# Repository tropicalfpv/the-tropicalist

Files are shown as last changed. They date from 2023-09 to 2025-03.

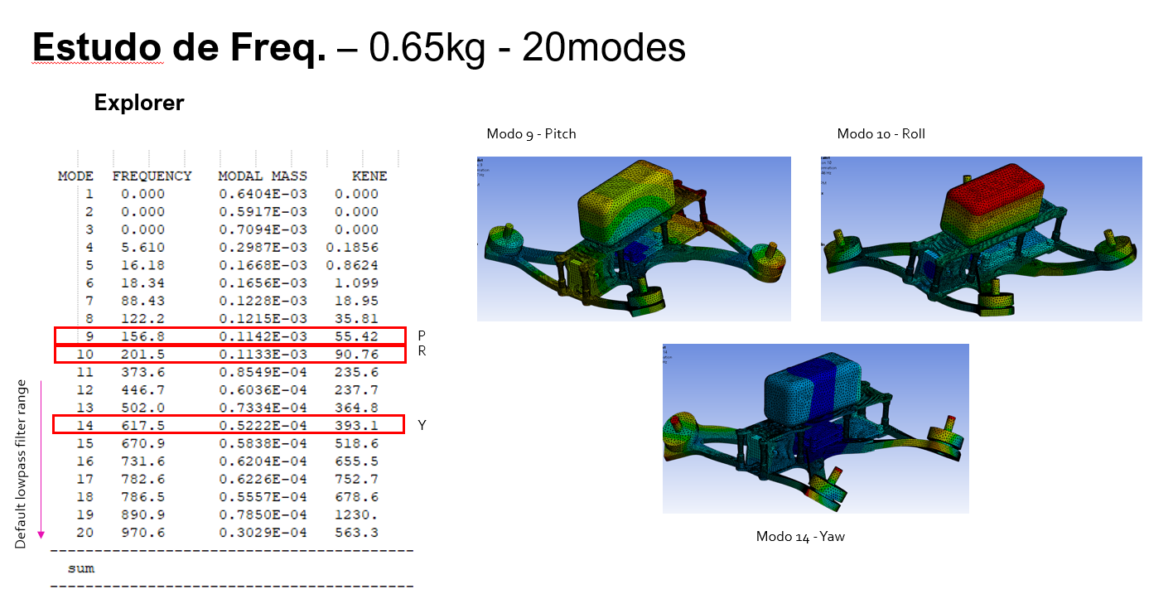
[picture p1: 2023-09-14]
Project/FEA Analysis/freq.PNG

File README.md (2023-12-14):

Capture

# The Tropicalist 5" FPV Open Source Frame Kit :bird:
Developed to be the best FPV frame in the world, no matter what is your application. Born in Brazil. Join the community for support, news, and other major releases, as well as to get help during your development [in our discord][7].

*PT_BR: Se você quer entender melhor do frame assim como seus aspectos principais, em portugês, acesse www.tropicalfpv.com*



## Quick Notice :dollar:
This project was initially close-source. We opened to be part of a greater achievement for the FPV community, as well as to expand reach and dissipate knowledge. By doing so, we lost a great share of revenue. To support its constant evolution, [consider a donation][1].

## Short Read :envelope:
This frame was developed to be easily assembled, strong, and accessible for any 5' FPV build. Focused on having a better performance than traditional frames concerning resonant frequencies, it is a great build for cinematics and freestyle pilots. 
1. Start by downloading the latest files under the [Releases][5] page,
2. You can order the parts to construct the frame using this [Bill of Materials and Ordering Instructions][6],
3. Follow the [instructions for fabrication][4]

## Long Read :book:

### Objectives and Configuration :dart:
The Tropicalist Frame Kit was initially developed in 2020 during the pandemic, during which a great flow of imports in Brazil was frozen. To keep the FPV rolling here, we needed a frame that could be strong enough to withstand the tropical bandos and also cinematic ready, since a new era of pilots was born.

The Frame is a perfect X configuration, has 5mm arms, and is designed for up to 5.1in props. It has enough space for analog and digital builds and it's designed to carry a camera on top, as well as a 4s-6s battery.

For the Frame to perform at its best, is expected that fabrication using 3K plain matte carbon, from a good supplier is used. If you are using other composites or materials be aware that it can be extremely poor on performance, since the materials' mechanical properties are key in this design.

### Editing and Modifying the Files :rocket:
You can modify and download the original Autodesk Fusion 3D Files. Those are available [here][8]. If you want to consider collaborating on this project, [please follow the guidelines here for contributing][2], and our step-by-step process to have PRs accepted.

### Scientific-Based Research :microscope:
The Tropicalist Frame is based on scientific research to approach a feasible, high-frequency resonant frame. It is also tested in Structural FEA Analysis Software (such as Ansys Mechanical) before being released. All major changes should include a FEA Analysis and field testing before being considered a new release under the main branch. We do this to guarantee the highest standard in design quality and best practices, so users and the community can rely on a frame without being super nerds about mechanical aspects. They just trust, and that´s enough :)



freq

## Licenses & Right to Use :closed_lock_with_key:
This project is licensed under the [Creative Commons Attribution-ShareAlike 4.0 International Public License][3]. This means that you can use, modify, and benefit from the project, including commercial use. This license, however, obligates you or any party to maintain the name of the product as copywriting and share any projects related to it under the same Open Source License. This means that if you use in part of your design, yours needs to be open source too.

## Found a Problem? :goberserk:
It's ok, you don't need to fix it, you can let us know to do so. Just [open an Issue here][9] and be detailed about what happened. 

[1]: https://patreon.com/TropicalFPV
[2]: https://github.com/tropicalfpv/the-tropicalist/blob/main/GUIDELINES.md
[3]: https://github.com/tropicalfpv/the-tropicalist/blob/main/LICENSE
[4]: https://github.com/tropicalfpv/the-tropicalist/blob/main/ASSEMBLY.md
[5]: https://github.com/tropicalfpv/the-tropicalist/releases
[6]: https://github.com/tropicalfpv/the-tropicalist/blob/main/BOM.md
[7]: https://discord.gg/JvUaVDHNnM
[8]: https://github.com/tropicalfpv/the-tropicalist/tree/main/Project/Fusion%203D%20Files
[9]: https://github.com/tropicalfpv/the-tropicalist/issues/new

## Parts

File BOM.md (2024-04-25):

# Bill of Materials and Ordering Instructions
You can buy using your favorite store/supplier. We recommend the following ones:
Please note that these are affiliate links. By using them, you help to support the project with a commission that has no additional cost to you :)

## Frame Cut Parts
Good-quality carbon is a must! We recommend Sunlike because they offer ready cuts, and use a great fiber+resin mix (3k plain matte). Email info@sunlikeec.com with a zip of the ['Latest Release of the Carbon Cut Files'][1] for a quote and then use this link to pay after the quote is sent to you: https://s.click.aliexpress.com/e/_Dlow8zd. You should select the amount of dollars that were quoted as the quantity of the items since each one is exactly one dollar. **You can also pay by PayPal, so you don't get a big amount in Aliexpress (mainly for Brazilian customers). Ask Sunlike for the instructions in your email**

PT_BR: Para detalhes sobre como comprar sem uma taxa abusiva do Remessa Conforme, me chame no insta @tropical.fpv

Example email asking for a quote:



## Hardware Parts
If you are using the affiliate links, please select the correct part after you are redirected.

- 8x M3x14mm Hex (https://s.click.aliexpress.com/e/_Dn0yasj)
- 8x M3x6mm Hex (https://s.click.aliexpress.com/e/_Dn0yasj)
- 4x M3x20mm Flathead Hex (stack option 1) (https://s.click.aliexpress.com/e/_DnrfiV5) 
- 4x M3x8mm Flathead Hex (stack option 2) (https://s.click.aliexpress.com/e/_DnrfiV5)
- 4x M3x16mm Hex (https://s.click.aliexpress.com/e/_Dn0yasj)
- 16x M3x8mm Hex (Motor Screws) (https://s.click.aliexpress.com/e/_DksbGjv)
- 4x 4x M3x6mm Flathead Hex (https://s.click.aliexpress.com/e/_DnrfiV5)
- 4x M3x30mm 6mm diameter Aluminium standoff (https://s.click.aliexpress.com/e/_DC3XDLV)
- 4x M3x35mm 6mm diameter Aluminium standoff (https://s.click.aliexpress.com/e/_DC3XDLV)
- 8x M3 Parlock Nut (https://s.click.aliexpress.com/e/_DDdlpIF)

## Cost (US Dollar)
The biggest cost is of the carbon fiber plates, mainly the arms.
- Carbon plates (entire kit for one frame): ~$58,00
- Hardware Kit (Standoffs): ~$6,00
- Hardware Kit (Screws): $5,00
- 3D printed parts: ~$8,00
- Shipping (CN to BR): ~$10,00
**Total Cost approximated is ~$89,00**

Depending on where you live, this can range up and down by about 15%.

[1]: [https://github.com/tropicalfpv/the-tropicalist/releases]

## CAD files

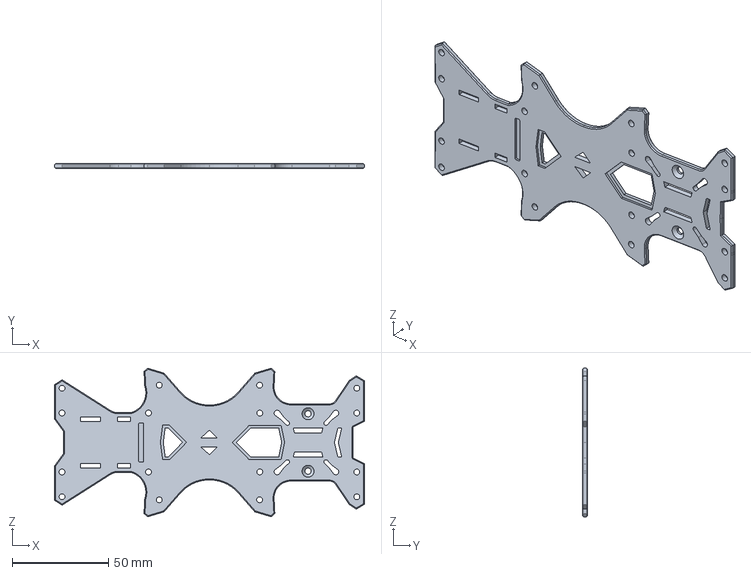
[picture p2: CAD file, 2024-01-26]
Project/Carbon Cut Files/2.5mm cut/bottom_plate_x1.step
161.3 x 2.50 x 77.3 mm

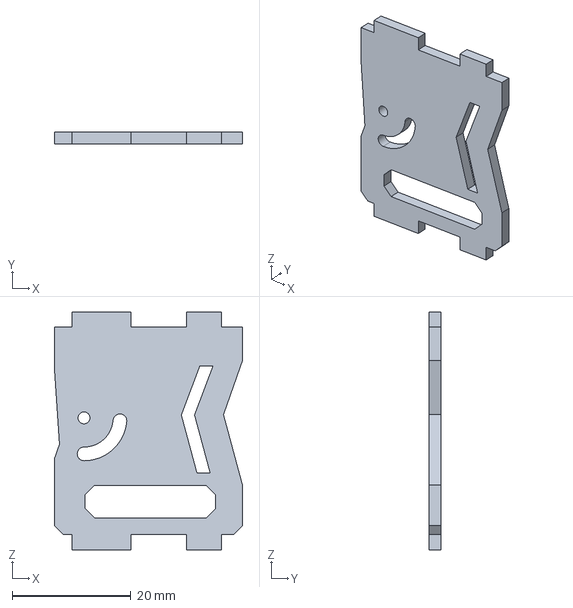
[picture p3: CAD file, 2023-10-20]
Project/Carbon Cut Files/2mm cut/camera_mount_side_plate_x2.step
31.7 x 2.00 x 40.1 mm

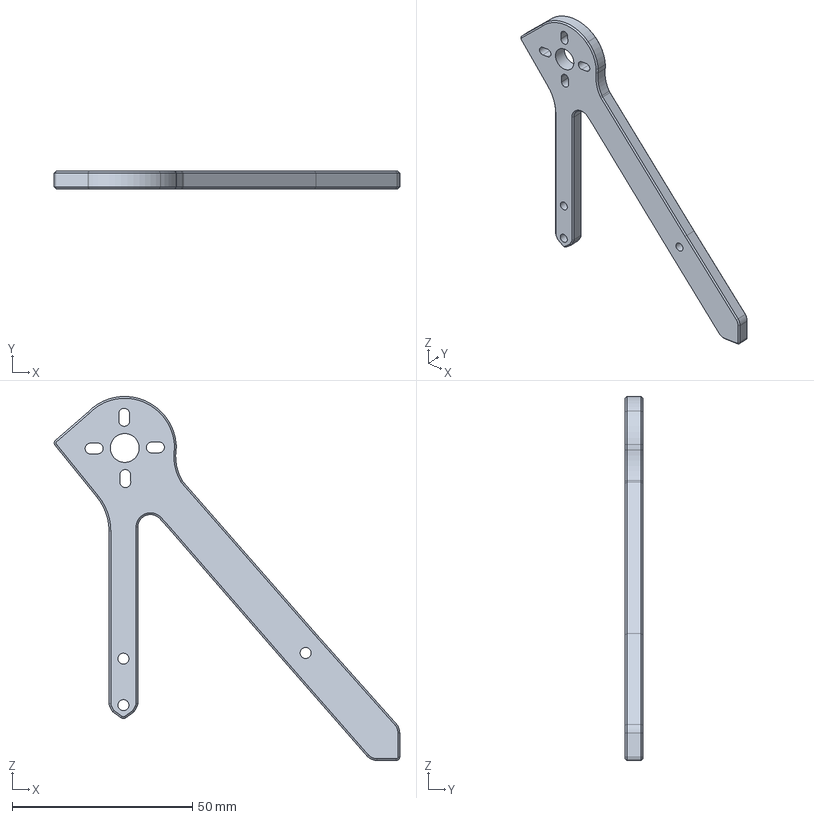
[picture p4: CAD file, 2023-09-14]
Project/Carbon Cut Files/5mm cut/arm_x4.step
95.9 x 5.00 x 101.0 mm

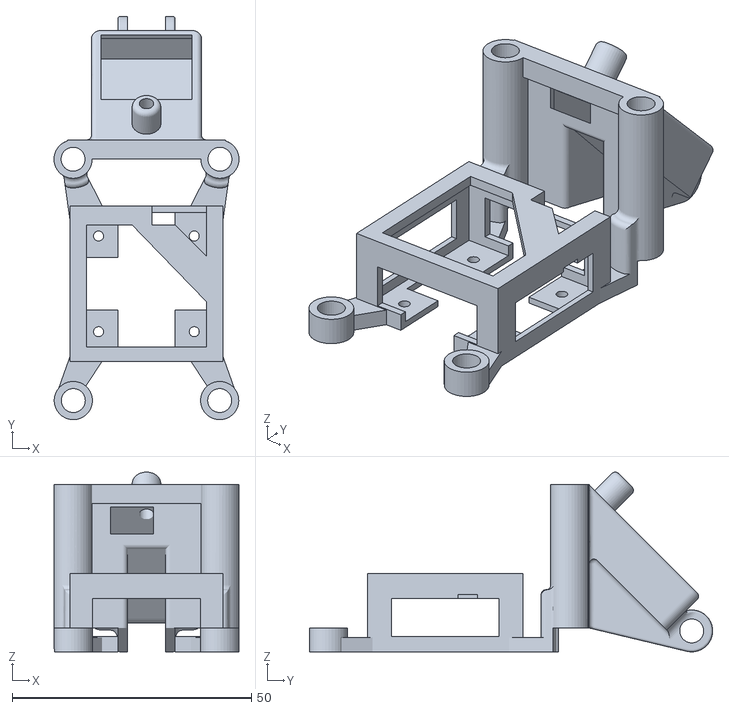
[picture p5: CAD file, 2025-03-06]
Project/STL Files/caddx_and_gpshold.STL
38.7 x 84.3 x 37.6

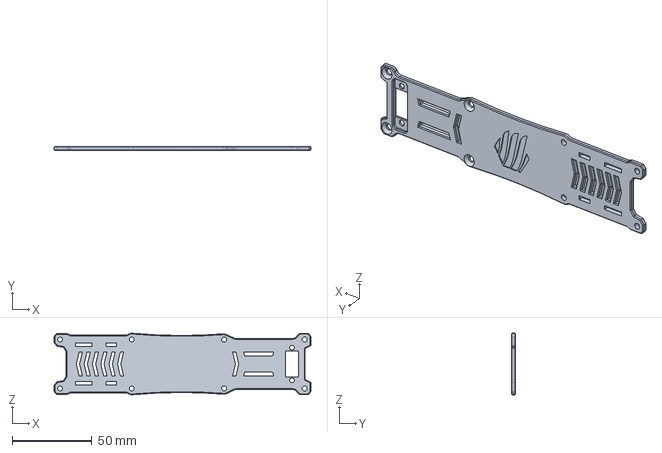
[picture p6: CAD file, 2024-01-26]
Project/Carbon Cut Files/2.5mm cut/top_plate_x1.step
161.2 x 2.50 x 38.7 mm

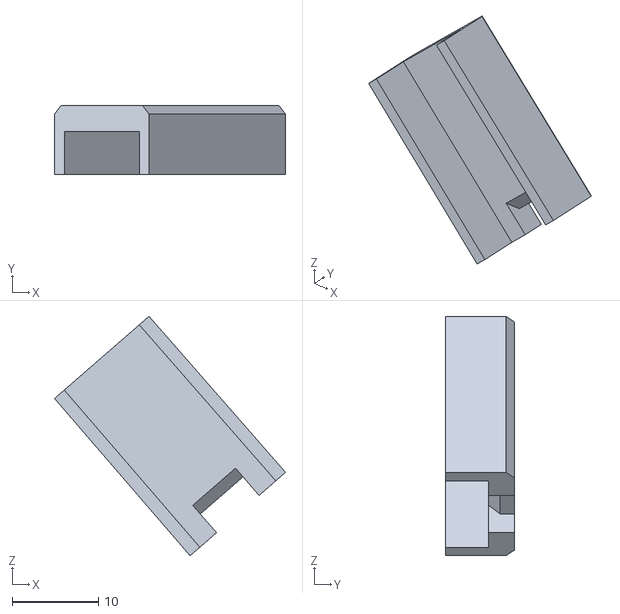
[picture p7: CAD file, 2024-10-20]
Project/STL Files/motor_wire_protector.stl
26.7 x 8.00 x 27.7

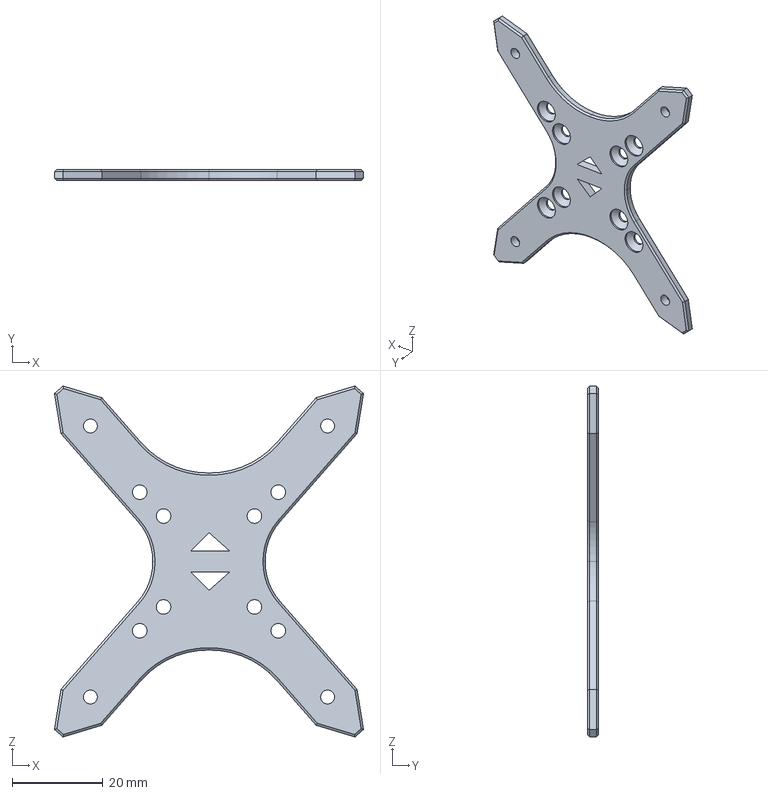
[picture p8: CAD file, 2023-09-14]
Project/Carbon Cut Files/2.5mm cut/middle_plate_x1.step
68.1 x 2.50 x 77.3 mm

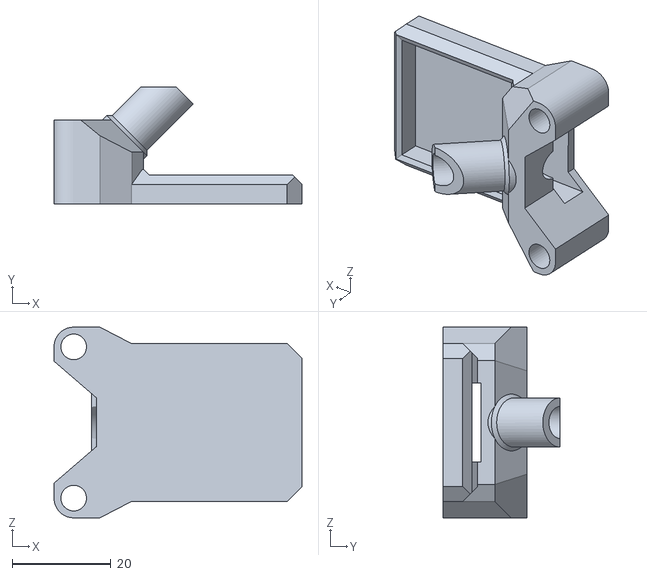
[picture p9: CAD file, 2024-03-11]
Project/STL Files/gps_antenna_mount_O3.stl
50.3 x 23.7 x 38.7

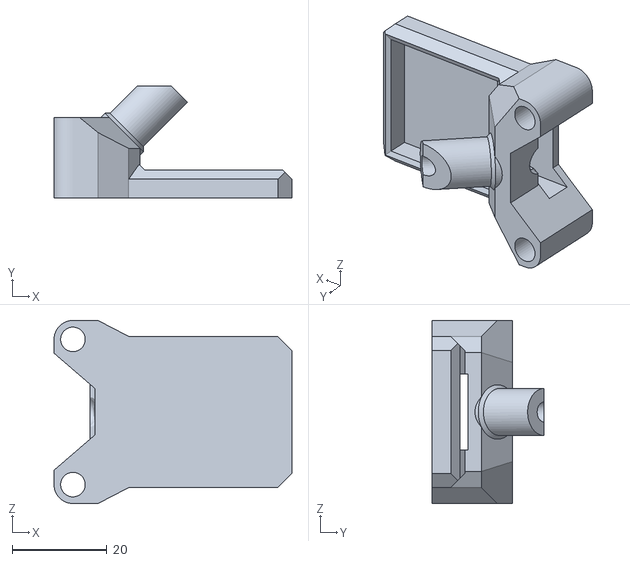
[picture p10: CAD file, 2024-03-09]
Project/STL Files/gps_antenna_mount_caddx_vista.stl
50.3 x 23.7 x 38.7

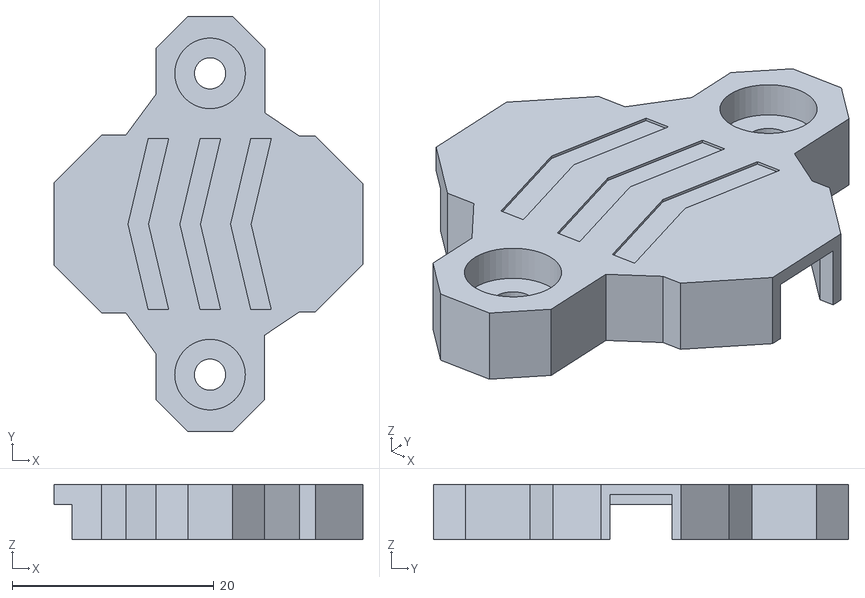
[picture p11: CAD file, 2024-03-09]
Project/STL Files/rx_holder_botom.stl
30.6 x 41.2 x 5.50

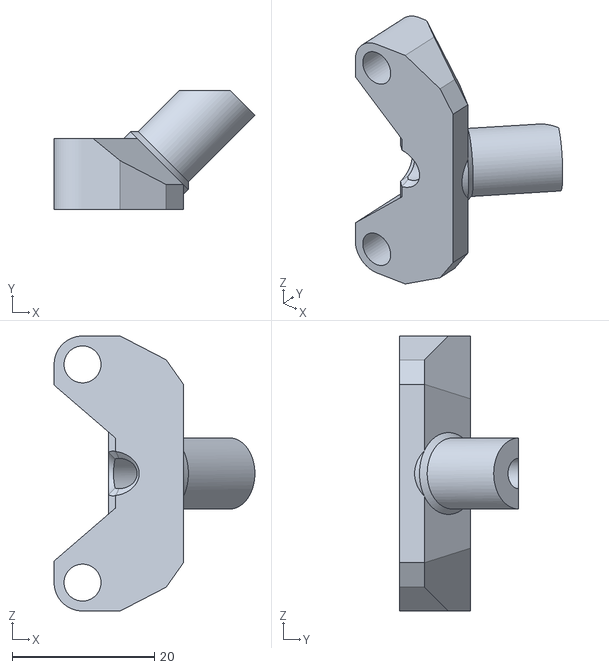
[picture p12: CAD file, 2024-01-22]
Project/STL Files/antenna_mount_caddx_vista.stl
28.3 x 16.7 x 38.7

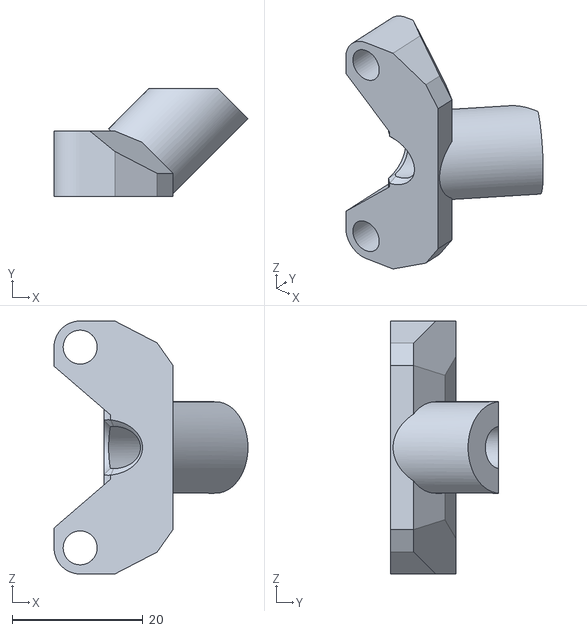
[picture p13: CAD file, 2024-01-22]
Project/STL Files/antenna_mount_O3.stl
29.7 x 16.5 x 38.7

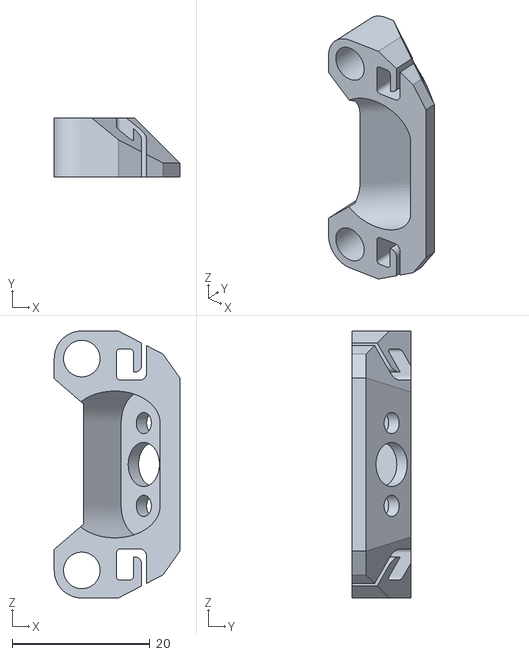
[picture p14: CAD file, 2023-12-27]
Project/STL Files/antenna_mount_sma.stl
18.2 x 8.50 x 38.7

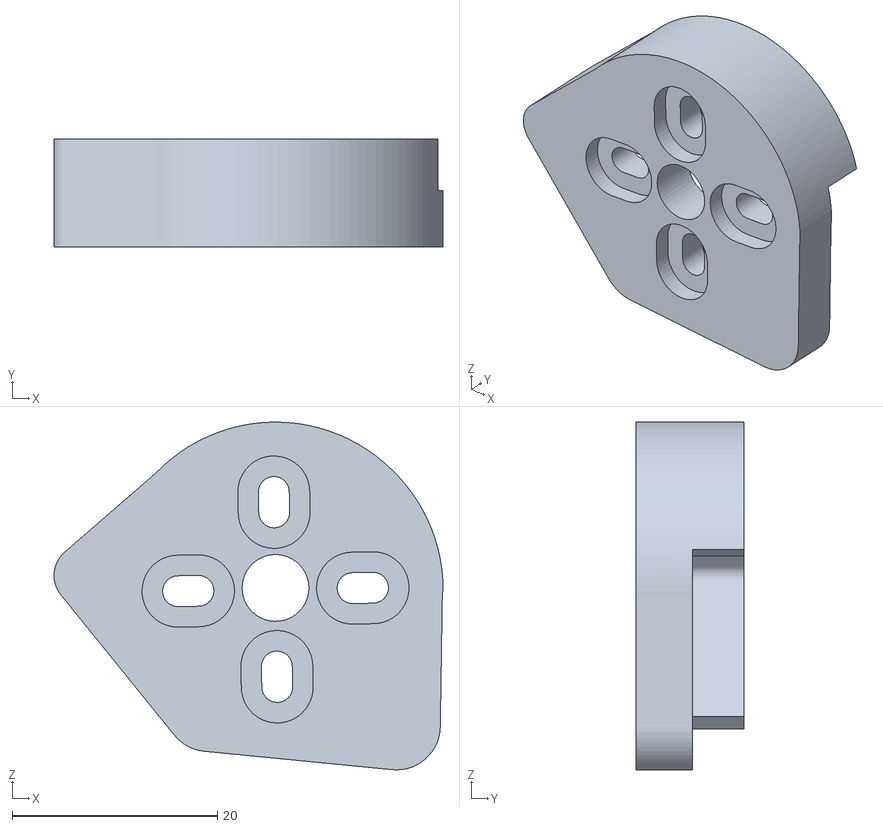
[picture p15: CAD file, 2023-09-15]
Project/STL Files/skids_protect_arms_clockwise.stl
37.9 x 10.5 x 33.9

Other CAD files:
Project/STL Files/skids_protect_arms_anticlockwise.stl
Project/STL Files/gopro_mount.stl
Project/Fusion 3D Files/arm.f3d
Project/Fusion 3D Files/bottom_plate.f3d
Project/Fusion 3D Files/fpv_camera_mount.f3d
Project/Fusion 3D Files/frame_standoff_long.f3d
Project/Fusion 3D Files/frame_standoff_short.f3d
Project/Fusion 3D Files/middle_plate.f3d
Project/Fusion 3D Files/top_plate.f3d

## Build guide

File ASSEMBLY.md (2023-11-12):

# Assembly Process of The Tropicalist

PT_BR - Se você está procurando instruções de montagem em portugês, voce pode encontrá-las [aqui][1]

If you want to build and assemble The Tropicalist frame yourself, follow these guidelines. The build is simple and pretty straightforward, so you should not have a complicated time doing it. 

**Do you already have everything? Check the [Bill of Materials][2] page for a list of components to buy.**

## Instructions
Follow this video with assembly instructions:
https://www.youtube.com/watch?v=X8bwbNJvkuo

## Components List
1. 1 Bottom Plate
2. 4 Arms
3. 1 Middle Plate (Stack Interface)
4. 2 Camera Supports
5. 1 Top Plate

## Hardware List
All screws are steel, standoffs and Nuts are Aluminium

- 8x M3x14mm Hex (https://s.click.aliexpress.com/e/_Dn0yasj)
- 8x M3x6mm Hex (https://s.click.aliexpress.com/e/_Dn0yasj)
- 4x M3x20mm Flathead Hex (stack option 1) (https://s.click.aliexpress.com/e/_DnrfiV5) 
- 4x M3x8mm Flathead Hex (stack option 2) (https://s.click.aliexpress.com/e/_DnrfiV5)
- 4x M3x16mm Hex (https://s.click.aliexpress.com/e/_Dn0yasj)
- 16x M3x8mm Hex (Motor Screws) (https://s.click.aliexpress.com/e/_DksbGjv)
- 4x M3x6mm Flathead Hex (https://s.click.aliexpress.com/e/_DnrfiV5)
- 4x M3x30mm 6mm diameter Aluminium standoff (https://s.click.aliexpress.com/e/_DC3XDLV)
- 4x M3x35mm 6mm diameter Aluminium standoff (https://s.click.aliexpress.com/e/_DC3XDLV)
- 8x M3 Parlock Nut (https://s.click.aliexpress.com/e/_DDdlpIF)

Additional screws may be needed if you want to fix other components, such as VTXs for example. The list below is not necessary, but may also help.

1. 4x M3x6mm Hex
2. 4x M2x8mm Hex

You can also have the 3D Prints as your choice, so check the 3D Prints Folder for Files that may help your build.

## Building Instructions

I'm still formatting for the new version, but you can see the pictures [here][1]

[1]: https://tropicalfpv.com/the-tropicalist-welcome/
[2]: https://github.com/tropicalfpv/the-tropicalist/blob/main/BOM.md

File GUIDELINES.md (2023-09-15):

sim

# Contribuition Guidelines
We truly believe that people who want to contribute to this project have the power, and freedom, to do so. To keep the best quality possible, we have made a guideline to ensure that we only go forward, not backward.
If you want to contribute to this project, please follow these guidelines to have your PR approved.

## General Guidelines
All PRs must include:
- A clear description of what the change was made, and why
- The benefits that will bring
- Change-log to the original
- Overall important details

### Frame Structure
Any major modification to the frame structure should include, at least:
- A clean and organized design in the fusion files
- The simulation results, if major changes are made (we can run those too if needed)
- Adaptation of additional files if modifications made influence them (e.g. adapt the design of 3D prints)

### Hardware and BOM
Any major modification to the hardware used should include, at least:
- The new configuration of the hardware changed
- A clear description of the material's properties
- The components must also be inserted into the design, for ease of use and a clear assemble process

### Simulation
If you run or modify any simulation, please include:
- Changes in material properties (if made)
- Changes in mechanical configuration (if made)
- Changes in additional files (if made)
- The simulation results
- The new simulation files
- A brief description of the process and objective of the simulation
- The category (if it is mechanical, fluid, harmonics, etc)

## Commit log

2023-09-14 First commit with production files
    Production files for the V3 model in STEP files used for cutting machines
    [arm.step, bottom_plate.step, camera_mount_side_plate.step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]
2023-09-14 Create BOM.md
    Initial bil of materials
2023-09-14 Update README.md
    add bill of materials
2023-09-14 Update the list of materials to buy
    Change the commit title to be readable from the main page
2023-09-14 Add tropicalist logo to main plate
    Add logo on top of the mais plate with -0.5mm cut
    [top_plate_x1.step]
2023-09-14 Organization cuts in folders
    Organized the folders by naming with the height of the cut
    [arm_x4.step, bottom_plate_x1.step, camera_mount_side_plate_x2.step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]
2023-09-15 Update ASSEMBLY.md
    corrected text
2023-09-15 Added bill of materials link.md
2023-09-15 Add 3D Files for the V3 Frame
    add the files stl for printing
    [gopro_mount.stl, skids_protect_arms_anticlockwise.stl, skids_protect_arms_clockwise.stl]
2023-09-16 Added original e editable fusin 3d files
    [arm.f3d, bottom_plate.f3z, fpv_camera_mount.f3d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]
2023-09-16 Corrected bottom plate extension and body file
    [bottom_plate.f3d]
2023-09-16 Added Zip file for carbon cut fast quotation
2023-09-18 Added antena mounts for the back standoffs
    [antenna_mount_O3.stl, antenna_mount_sma.stl]
2023-10-20 Lowered top fix for realeasing tension on top plate
    Lowered size to fit tight to the new 2.5mm top plate and aligned standoff so no material tension is created when tightening top plate screws as a result of dimension discrepancy
    [fpv_camera_mount.f3d]
2023-10-20 Fix bottom plate overall functionalities
    Added two back screws placement for RX holder outside the bottom frame, while adding back space for the wires to run into the frame. Also made the VTX fixing back part screw slidable. Changed the version number on the bottom part of the plate.
    [bottom_plate.f3d]
2023-10-20 Updated size
    [camera_mount_side_plate_x2.step]
2023-10-20 Updated minor improvements
    [bottom_plate_x1.step]
2023-10-23 Fixed 30.5x30.5 back mounting holes
    fixed a small % of error in the mounting holes at the back part of the frame for the 30.5x30.5s
    [bottom_plate.f3d]
2023-10-23 Fixed 30.5x30.5 back mounting holes
    [bottom_plate_x1.step]
2023-10-23 Adjusted cut files for the latest design
2023-10-24 Update ASSEMBLY with instructions video
2023-12-21 Added RX holder to the bottom part of the frame
    [rx_holder_botom.stl]
2023-12-21 Added mounting holes for RX support
    Now you can mount your RX in the back bottom part of the frame using the RX 3d printed holder
    [bottom_plate.f3d]
2023-12-21 New O3 Antenna Mount 3d print
    [antenna_mount_O3.stl]
2023-12-21 Added new tpu vista antenna mount
    [antenna_mount_caddx_vista.stl]
2023-12-21 New bottom plate cut adjusted for rx support
    [bottom_plate_x1.step]
2023-12-21 New cut files for latest release
2023-12-24 Added SMA antenna mount STL
    [antenna_mount_sma.stl]
2023-12-27 New Spacing for XFIRE L shape RX Antenna
    [antenna_mount_sma.stl]
2024-01-22 Delete Project/3D Files directory
    Deleted for full update
    [antenna_mount_O3.stl, antenna_mount_caddx_vista.stl, antenna_mount_sma.stl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]
2024-01-22 Added latest release STL files folder
    [antenna_mount_O3.stl, antenna_mount_caddx_vista.stl, antenna_mount_sma.stl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]
2024-01-26 Adjusted XT60E-M spacing
    [top_plate_x1.step]
2024-01-26 Rmoved tension corners
    Removed tension corners as reported by AbuFPV on the front part of the frame
    [bottom_plate_x1.step]
2024-01-26 Added new plates to the cut files
2024-03-09 Added STL Files for GPS Suport and SuperD ERLS RX
    [gps_antenna_mount_caddx_vista.stl, rx_holder_botom.stl]
2024-03-09 New Carbon Cut Files
2024-03-11 O3 with GPS mounting 3D Print
    [gps_antenna_mount_O3.stl]
2024-04-25 Update BOM.md with new Sunlike email
2024-10-20 Added motor wire protector STL
    [motor_wire_protector.stl]
2025-03-06 added caddx and gps holder STL by @fpv_fernando
    [caddx_and_gpshold.STL]
